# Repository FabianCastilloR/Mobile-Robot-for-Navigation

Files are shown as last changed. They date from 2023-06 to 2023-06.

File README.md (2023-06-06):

# Mobile Robot for Navigation Tasks with Obstacle Avoidance using Potential Fields

This project implements a mobile robot capable of performing navigation tasks in an environment with obstacles using the potential fields algorithm. The robot is designed to autonomously move towards a goal location while avoiding obstacles in its path.

## Table of Contents

- [Introduction](#introduction)
- [Installation](#installation)
- [Usage](#usage)
- [Algorithm](#algorithm)
- [Demo](#demo)

## Introduction

The goal of this project is to develop a mobile robot that can navigate through an environment by employing the potential fields algorithm. The robot uses an ESP32 (programmed in Arduino IDE) as an UDP server that receives data from a PC client connected to a camera that's visualizing a workspace and sends the data necessary to detect obstacles in its surroundings. The PC client is programmed in Python. By calculating attractive and repulsive forces from the goal location and obstacles, respectively, the robot can plan its path and avoid collisions.

## Installation

1. Clone the repository:

   ```bash
   git clone https://github.com/FabianCastilloR/Mobile-Robot-for-Navigation.git
   ```

2. Install the necessary dependencies in python's PC client:

   ```bash
   pip install matplotlib
   pip install numpy
   pip install opencv-contrib-python
   ```

3. Install the necessary libraries and boards in Arduino IDE:

   ```bash
   Libraries:

   MPU6050.h from https://github.com/jrowberg/i2cdevlib/tree/master/Arduino/MPU6050

   I2Cdev.h from https://github.com/jrowberg/i2cdevlib/tree/master/Arduino/I2Cdev

   Wifi.h from Arduino IDE Library Manager

   Boards:

   ESP32 from https://dl.espressif.com/dl/package_esp32_index.json

   You can add the ESP32 board to Arduino IDE by going to File > Preferences > Additional Boards Manager URLs and adding the link above.
   ```

4. Configure the robot hardware by connecting sensors and actuators appropriately.

   ```bash
   The robot hardware consists of the following components:

    - ESP32 microcontroller

    - MPU6050 IMU

    - 4 DC motors with incremental encoders (In this project we use 2 microgeared motors of 6VDC at 100RPM and 2 microgeared motors of 6VDC at 50RPM, both with 14 CPR encoders)

    - 2 motor drivers (In this project we use 2 VNH2SP30 motor drivers)

    - 1 LiPo battery (In this project we use a 3S 11.1V 2200mAh LiPo battery)

    - 1 5V voltage regulator (In this project we use a XL4005 voltage regulator)

    - 1 6V voltage regulator (In this project we use a LM2596 voltage regulator)
    
    - 1 camera (In this project we use a Razer Kiyo X camera)
   ```

5. Configure the robot software by setting the appropriate parameters in the PC_Client_WMultipleObstacles.py file.

## Usage

1. Launch the robot navigation python program:

   ```bash
   python PC_Client_WMultipleObstacles.py
   ```

2. Launch the robot navigation program in Arduino IDE:

   ```bash
    ESP32_Server_WMultipleObstacles.ino
    ```

3. Set the goal location for the robot manually.

4. Set the obstacles in the workspace manually.

5. Observe the robot's movement and obstacle avoidance behavior in the environment.

## Algorithm

The potential fields algorithm works by simulating forces acting on the robot. The robot experiences an attractive force towards the goal location and repulsive forces from nearby obstacles. By summing these forces and calculating the resultant direction, the robot can navigate towards the goal while avoiding obstacles.

The algorithm consists of the following steps:

1. Obtain the position of the robot, goal and obstacles from the artificial vision system to detect and measure the distance from the robot to the goal location and to the obstacles.

2. Calculate the attractive force towards the goal location based on the current position.

3. Calculate the repulsive forces from nearby obstacles based on their positions and distances.

4. Sum the attractive and repulsive forces to obtain the resultant force vector.

5. Update the robot's velocity and heading based on the resultant force.

6. Repeat the process iteratively to navigate towards the goal while avoiding obstacles.

## Demo

Demonstration videos of the robot's navigation capabilities can be found here:
- [Mobile Robot for Navigation Tasks with Potential Fields Demo 1](https://youtu.be/NOnhNL_rm1k)    
- [Mobile Robot for Navigation Tasks with Potential Fields Demo 2](https://youtube.com/shorts/4KPQuJDRXes?feature=share)

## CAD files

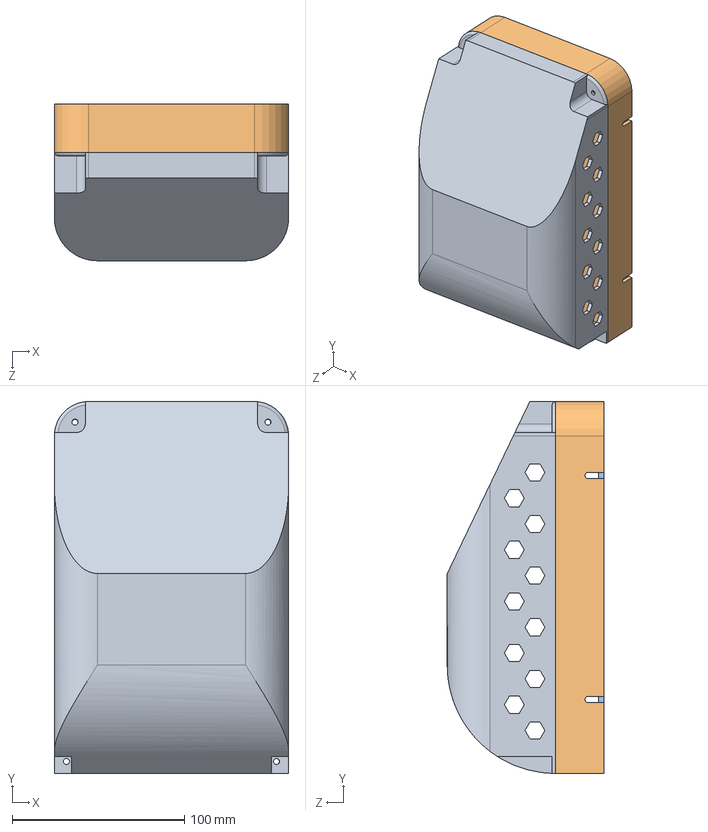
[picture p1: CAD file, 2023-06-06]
Mobile Robot CAD/Robot-Assembly.SLDASM
136.2 x 216.2 x 91.0 mm

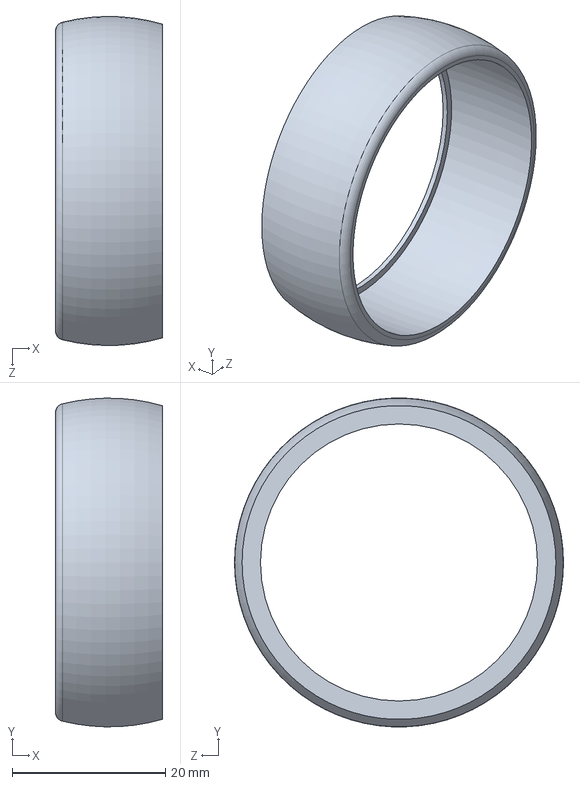
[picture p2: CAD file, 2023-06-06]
Mobile Robot CAD/Wheel.SLDPRT
14.0 x 43.0 x 43.0 mm

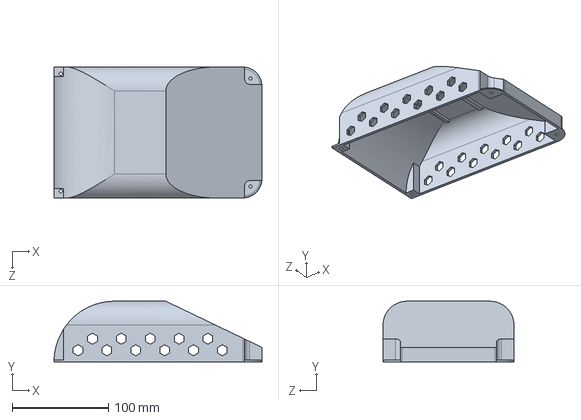
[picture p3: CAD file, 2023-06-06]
Mobile Robot CAD/Part3.SLDPRT
216.2 x 63.0 x 136.2 mm

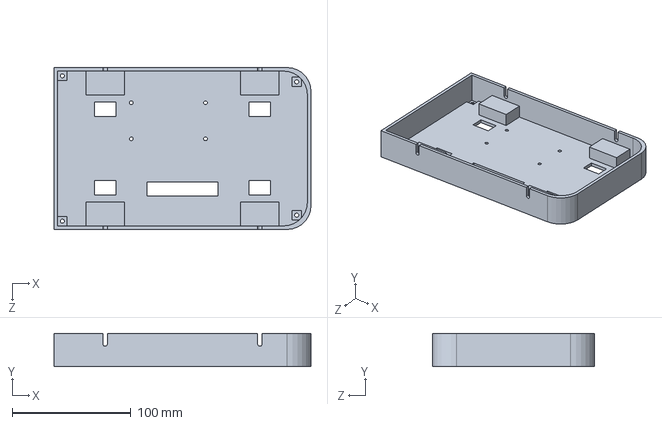
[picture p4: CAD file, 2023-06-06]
Mobile Robot CAD/Part2.SLDPRT
216.2 x 28.0 x 136.2 mm

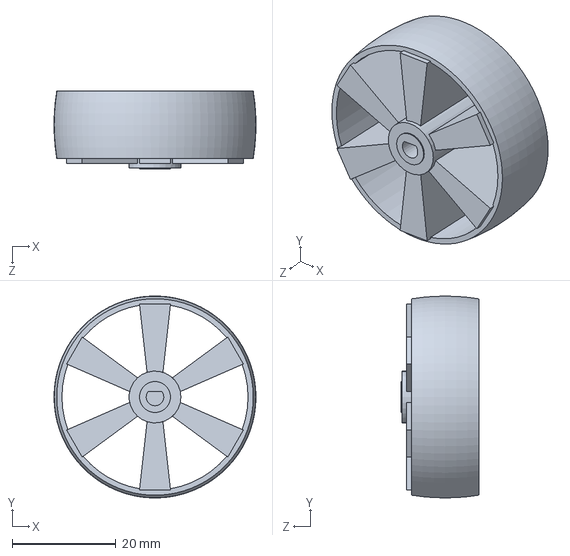
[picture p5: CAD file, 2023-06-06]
Mobile Robot CAD/Wheel-Rim.SLDPRT
38.9 x 38.9 x 15.0 mm

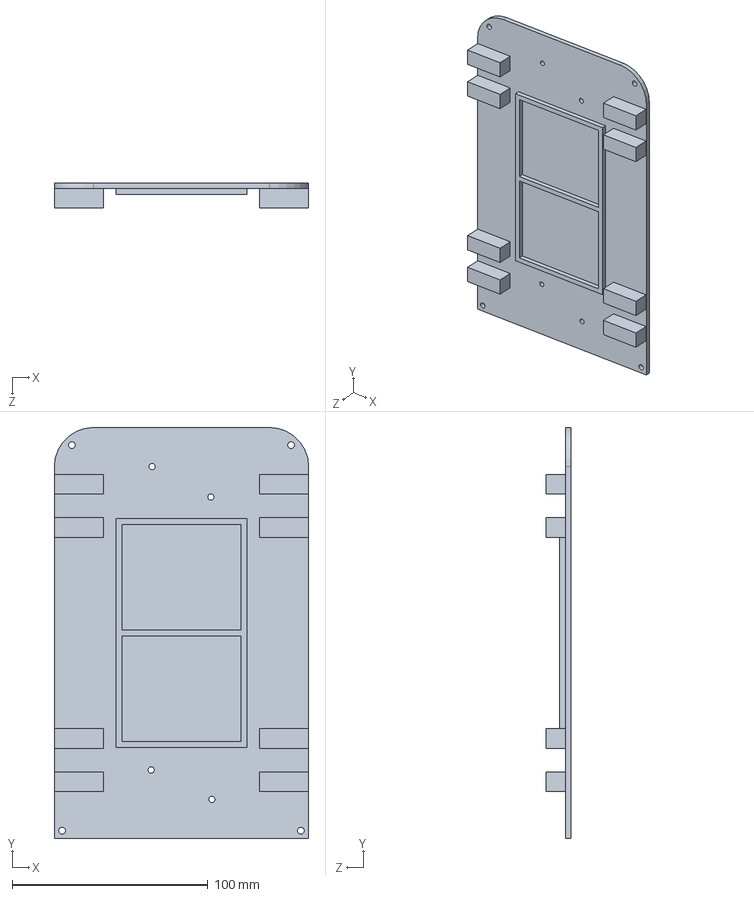
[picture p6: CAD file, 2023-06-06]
Mobile Robot CAD/Part1.SLDPRT
130.0 x 210.0 x 13.0 mm

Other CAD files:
Mobile Robot CAD/Part1.STL
Mobile Robot CAD/Part2.STL
Mobile Robot CAD/Part3.STL

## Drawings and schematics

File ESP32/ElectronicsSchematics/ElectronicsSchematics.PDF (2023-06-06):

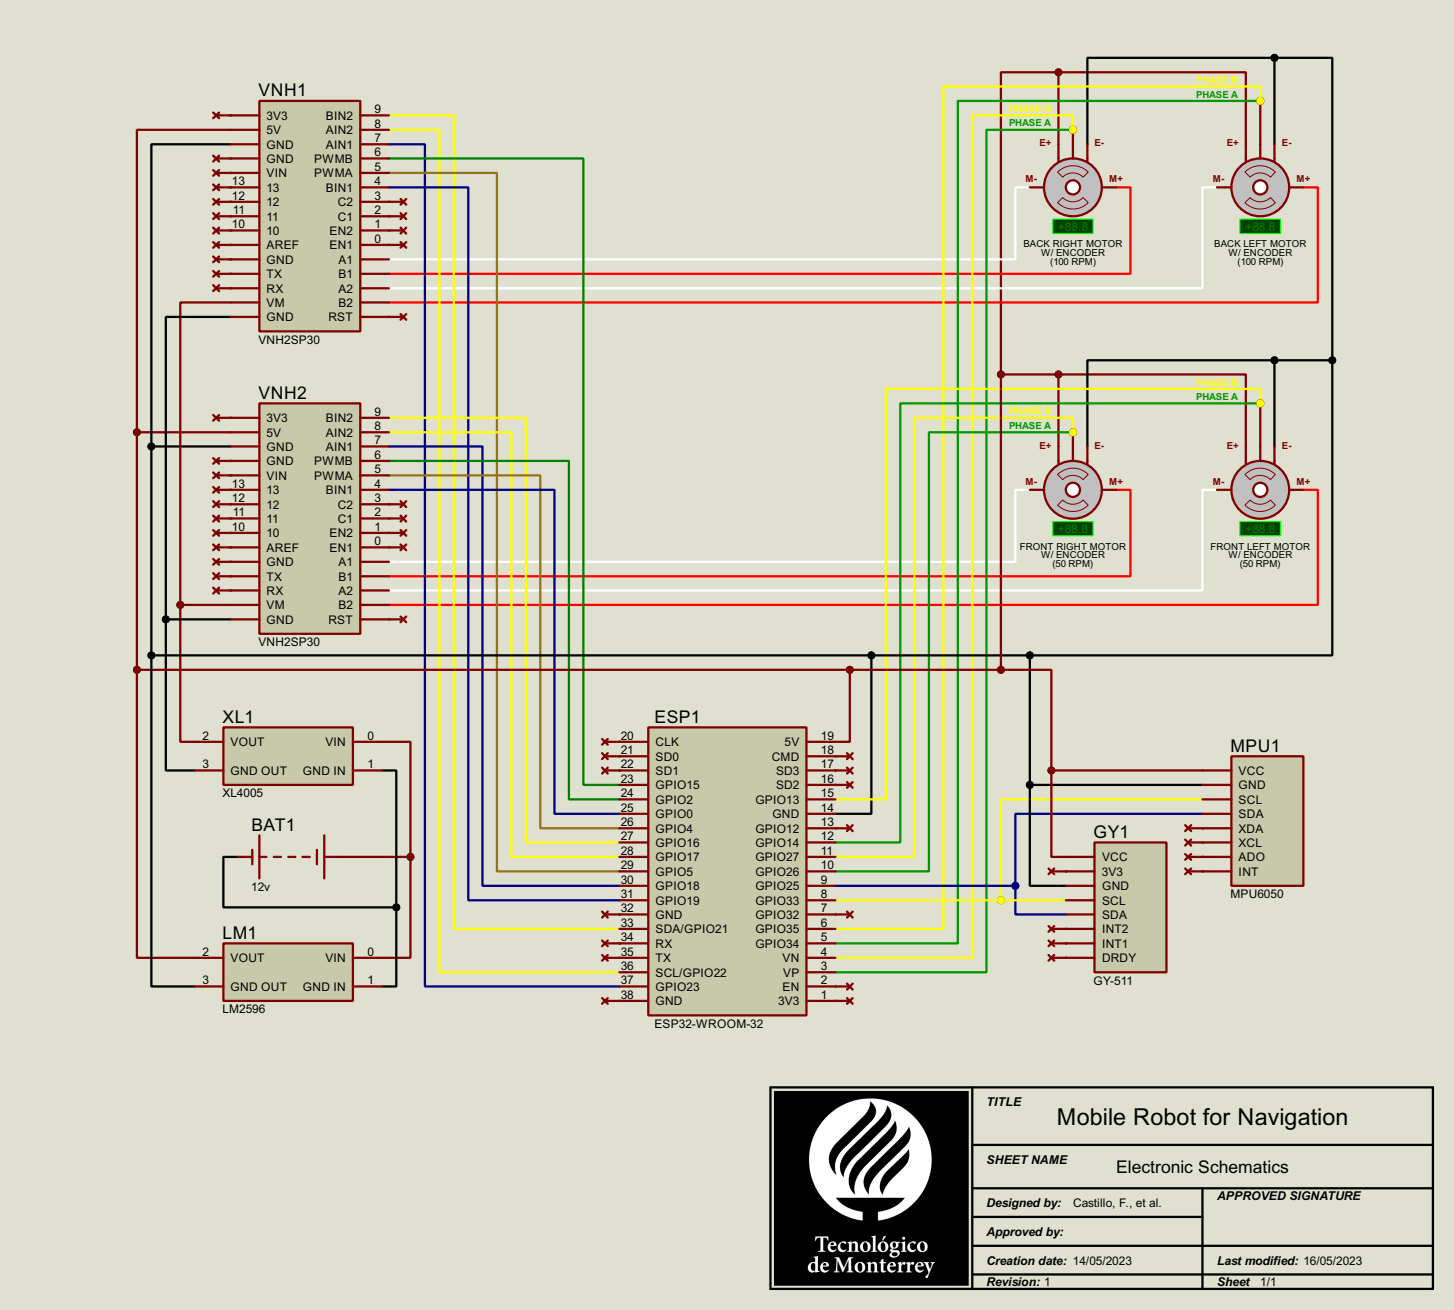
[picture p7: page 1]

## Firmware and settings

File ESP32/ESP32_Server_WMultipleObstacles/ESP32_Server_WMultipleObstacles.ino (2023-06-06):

// ESP32_Server_WMultipleObstacles.ino >

/*
Authors: F. Castillo-Rodríguez, S. Almaguer-Martínez, E. Silva-Estevez & A. Saavedra-Ricalde
Date: 2023/06/06
For Instituto Tecnológico y de Estudios Superiores de Monterrey, Campus Estado de México
Project: "Mobile Robot for Navigation Tasks"

Description:

This code is the server for the mobile robot. The communication between the client and the server is through UDP protocol.
This code receives the position (x, y) in cm of the robot, the goal and the obstacles from the client and uses it to 
determine the speed of the motors through the analysis of its kinematics. This case uses the form 
qd = J^-1 * (K1 * vti + K2 * vijo) where qd is the desired speed of the motors (linear and angular), J is the Jacobian 
matrix, vti is the speed vector of the robot and vijo is the sum of the speed vectors of each obstacle. 

For the obstacle avoidance, the robot uses the potential field method, where the robot is attracted to the goal and
repelled by the obstacles. The robot also uses a PID controller to control the speed of the motors.

The robot uses the gyroscope MPU6050 to determine its yaw angle and the encoders to determine its linear speed. It also
uses the Monster Motor Shield to control the motors. 

This code works only with Python's client code "PC_Client_WMultipleObstacles.py". To take into account only one obstacle,
the user must use the server code "ESP32_Server_WOneObstacle.ino" with the client code "PC_Client_WOneObstacle.py". To skip
obstacle avoidance, the user must use the server code "ESP32_Server_WNoObstacles.ino" with the client code 
"PC_Client_WNoObstacles.py".
*/

#include <WiFiUdp.h>
#include <MPU6050.h>  // From: https://github.com/jrowberg/i2cdevlib/tree/master/Arduino/MPU6050
#include <I2Cdev.h>   // From: https://github.com/jrowberg/i2cdevlib/tree/master/Arduino/I2Cdev
#include <Wire.h>
#include <WiFi.h>
#include <math.h>
#include <stdlib.h>

// Front right and left motor 50 RPM (298:1 reductor)
// Back right and left motor 100 RPM (149:1 reductor)

///////////////////////////////////////////////////////// Variables /////////////////////////////////////////////////////////////////////

// Define PWM pins for motors
const int motorPWMFL = 2;   // PIN 6 FRONT MOTOR SHIELD TO PIN 2 ESP32 // GREEN
const int motorPWMFR = 4;   // PIN 5 FRONT MOTOR SHIELD TO PIN 4 ESP32 // BROWN
const int motorPWMBL = 15;  // PIN 6 BACK MOTOR SHIELD TO PIN 15 ESP32 // GREEN
const int motorPWMBR = 5;   // PIN 5 BACK MOTOR SHIELD TO PIN 5 ESP32 // BROWN

// Define direction of wheels pins
const int dirFrontMFL = 0;   // PIN 4 FRONT MOTOR SHIELD TO PIN 0 ESP32 // BLUE
const int dirBackMFL = 16;   // PIN 9 FRONT MOTOR SHIELD TO PIN 16 ESP32 // YELLOW
const int dirFrontMFR = 17;  // PIN 8 FRONT MOTOR SHIELD TO PIN 17 ESP32 // YELLOW
const int dirBackMFR = 18;   // PIN 7 FRONT MOTOR SHIELD TO PIN 18 ESP32 // BLUE
const int dirFrontMBL = 19;  // PIN 4 BACK MOTOR SHIELD TO PIN 19 ESP32 // BLUE
const int dirBackMBL = 21;   // PIN 9 BACK MOTOR SHIELD TO PIN 21 ESP32 // YELLOW
const int dirFrontMBR = 22;  // PIN 8 BACK MOTOR SHIELD TO PIN 22 ESP32 // YELLOW
const int dirBackMBR = 23;   // PIN 7 BACK MOTOR SHIELD TO PIN 23 ESP32 // BLUE

// Define encoder pins
const int encoderMFL1 = 13;  // YELLOW
const int encoderMFL2 = 14;  // GREEN
const int encoderMFR1 = 27;  // YELLOW
const int encoderMFR2 = 26;  // GREEN
const int encoderMBL1 = 35;  // YELLOW
const int encoderMBL2 = 34;  // GREEN
const int encoderMBR1 = 39;  // VN PIN; YELLOW
const int encoderMBR2 = 36;  // VP PIN; GREEN

// Variables for PWM dispatch
const int pwmFrequency = 20000;  // The frequency managed by Monster Motor Shield is 20kHz
const int pwmResolution = 8;     // With a resolution of 8-bits the value goes from 0 - 255
const int pwmChannelMFL = 0;
const int pwmChannelMFR = 2;
const int pwmChannelMBL = 1;
const int pwmChannelMBR = 3;
int pwmMFL, pwmMFR, pwmMBL, pwmMBR;

// Variables for WiFi connection
WiFiUDP udp;
const char* ssid = "Conectate y di que eres mi perra";  // Your network SSID (name)
const char* password = "soytuperra";                    // Your network password
unsigned int localUdpPort = 4210;                       // Local port to listen on
char incomingPacket[1024];                              // Buffer to hold incoming packet
char buf[255];                                          // Buffer to hold outgoing packet

// Variables for yaw detection through the gyroscope
MPU6050 accgyro;
int16_t gx, gy, gz;
double gyroYaw = 0, gyroYawRad = 0, prevdTGyro = 0;

// Variables for robot's position control
double hxRobCM = 0, hyRobCM = 0, hxGoalCM = 0, hyGoalCM = 0, hxObsCM = 0, hyObsCM = 0;
int isRobot = 0, isGoal = 0, isObstacle = 0, numObs = 0;
const int maxObs = 50;
double hxMObsCM[maxObs], hyMObsCM[maxObs], hxyObsCM[maxObs * 2], vijoMag[maxObs], posObs[maxObs][2];
char hxyObsCMChar[1024];
char* variables;

// Variables for speed adcquisition
double speedRPMMFL = 0, speedRPMMFR = 0, speedRPMMBL = 0, speedRPMMBR = 0;
double speedRadSMFL = 0, speedRadSMFR = 0, speedRadSMBL = 0, speedRadSMBR = 0;
volatile int prevEncodedMFL = 0, prevEncodedMFR = 0, prevEncodedMBL = 0, prevEncodedMBR = 0;
volatile double encoderValueMFL = 0, encoderValueMFR = 0, encoderValueMBL = 0, encoderValueMBR = 0;
double prevEncoderValueMFL = 0, prevEncoderValueMFR = 0, prevEncoderValueMBL = 0, prevEncoderValueMBR = 0;
double prevMillisMFL = 0, prevMillisMFR = 0, prevMillisMBL = 0, prevMillisMBR = 0;

// Variables for PID controller
double kpMFL = 6.50, kpMFR = 15.00, kpMBL = 6.50, kpMBR = 6.50;
double kiMFL = 0.00275, kiMFR = 0.0038, kiMBL = 0.00275, kiMBR = 0.002;
double kdMFL = 5.51, kdMFR = 6.46, kdMBL = 5.51, kdMBR = 0.20;
double desiredSpeedRPMMFL = 0, desiredSpeedRPMMFR = 0, desiredSpeedRPMMBL = 0, desiredSpeedRPMMBR = 0;
double integralMFL = 0, integralMFR = 0, integralMBL = 0, integralMBR = 0;
double prevErrorMFL = 0, prevErrorMFR = 0, prevErrorMBL = 0, prevErrorMBR = 0;
int prevPIDMFL = 0, prevPIDMFR = 0, prevPIDMBL = 0, prevPIDMBR = 0;
double prevdTMFL = 0, prevdTMFR = 0, prevdTMBL = 0, prevdTMBR = 0;

/////////////////////////////////////////////////////////////////////////////////////////////////////////////////////////////////////////


///////////////////////////////////////////////////////// Program Setup /////////////////////////////////////////////////////////////////

void setup() {
  Serial.begin(115200);  // Begin serial communication at 115200 baud rate
  Wire.begin(25, 33);    // Begin I2C communication with pins SDA = 25 (Blue) and SCL = 33 (Yellow)

  // Enable encoder pins as inputs
  pinMode(encoderMFL1, INPUT);
  pinMode(encoderMFL2, INPUT);
  pinMode(encoderMFR1, INPUT);
  pinMode(encoderMFR2, INPUT);
  pinMode(encoderMBL1, INPUT);
  pinMode(encoderMBL2, INPUT);
  pinMode(encoderMBR1, INPUT);
  pinMode(encoderMBR2, INPUT);

  // Enable direction of the wheels pins as outputs
  pinMode(dirFrontMFL, OUTPUT);
  pinMode(dirBackMFL, OUTPUT);
  pinMode(dirFrontMFR, OUTPUT);
  pinMode(dirBackMFR, OUTPUT);
  pinMode(dirFrontMBL, OUTPUT);
  pinMode(dirBackMBL, OUTPUT);
  pinMode(dirFrontMBR, OUTPUT);
  pinMode(dirBackMBR, OUTPUT);

  // Configure LED PWM functionalitites
  ledcSetup(pwmChannelMFL, pwmFrequency, pwmResolution);
  ledcSetup(pwmChannelMFR, pwmFrequency, pwmResolution);
  ledcSetup(pwmChannelMBL, pwmFrequency, pwmResolution);
  ledcSetup(pwmChannelMBR, pwmFrequency, pwmResolution);

  // Attach the channel to the GPIO to be controlled
  ledcAttachPin(motorPWMFL, pwmChannelMFL);
  ledcAttachPin(motorPWMFR, pwmChannelMFR);
  ledcAttachPin(motorPWMBL, pwmChannelMBL);
  ledcAttachPin(motorPWMBR, pwmChannelMBR);

  // Interruptions of pulse detection of the encoders
  attachInterrupt(encoderMFL1, updateEncoderMFL, CHANGE);
  attachInterrupt(encoderMFL2, updateEncoderMFL, CHANGE);
  attachInterrupt(encoderMFR1, updateEncoderMFR, CHANGE);
  attachInterrupt(encoderMFR2, updateEncoderMFR, CHANGE);
  attachInterrupt(encoderMBL1, updateEncoderMBL, CHANGE);
  attachInterrupt(encoderMBL2, updateEncoderMBL, CHANGE);
  attachInterrupt(encoderMBR1, updateEncoderMBR, CHANGE);
  attachInterrupt(encoderMBR2, updateEncoderMBR, CHANGE);

  // Connect to WiFi
  Serial.printf("Connecting to %s ", ssid);
  WiFi.begin(ssid, password);  // Connect to the network
  // Wait for connection
  while (WiFi.status() != WL_CONNECTED) {
    delay(500);
    Serial.print(".");
  }
  Serial.println(" CONNECTED");
  // Print local IP address and start web server
  udp.begin(localUdpPort);
  Serial.printf("UDP Server IP: %s, UDP Server Port: %d\n", WiFi.localIP().toString().c_str(), localUdpPort);

  // Initialize gyroscope
  accgyro.initialize();
}

/////////////////////////////////////////////////////////////////////////////////////////////////////////////////////////////////////////


////////////////////////////////////////////////////////// Main Loop ////////////////////////////////////////////////////////////////////

void loop() {
  // Get the gyroscope values
  getGyroscope();
  gyroYawRad = -(gyroYaw * PI / 180);  // Convert yaw angle to radians

  // Get the speed of the wheels in RPM and rad/s with a sampling time of 50 ms
  double currentMillis = millis();
  if (currentMillis - prevMillisMFL >= 50) {
    speedRPMMFL = (-(encoderValueMFL - prevEncoderValueMFL) / ((currentMillis - prevMillisMFL) / 60000)) / (297.9238 * 14 * 2);
    speedRadSMFL = speedRPMMFL * (PI / 30);
    prevEncoderValueMFL = encoderValueMFL;
    prevMillisMFL = currentMillis;
  }
  if (currentMillis - prevMillisMFR >= 50) {
    speedRPMMFR = ((encoderValueMFR - prevEncoderValueMFR) / ((currentMillis - prevMillisMFR) / 60000)) / (297.9238 * 14 * 2);
    speedRadSMFR = speedRPMMFR * (PI / 30);
    prevEncoderValueMFR = encoderValueMFR;
    prevMillisMFR = currentMillis;
  }
  if (currentMillis - prevMillisMBL >= 50) {
    speedRPMMBL = (-(encoderValueMBL - prevEncoderValueMBL) / ((currentMillis - prevMillisMBL) / 60000)) / (297.9238 * 14);
    speedRadSMBL = speedRPMMBL * (PI / 30);
    prevEncoderValueMBL = encoderValueMBL;
    prevMillisMBL = currentMillis;
  }
  if (currentMillis - prevMillisMBR >= 50) {
    speedRPMMBR = ((encoderValueMBR - prevEncoderValueMBR) / ((currentMillis - prevMillisMBR) / 60000)) / (297.9238 * 14);
    speedRadSMBR = speedRPMMBR * (PI / 30);
    prevEncoderValueMBR = encoderValueMBR;
    prevMillisMBR = currentMillis;
  }

  // Send an empty package to the server to request the variables
  sendPackagesUDP(buf);

  // Receive the variables from the server
  variables = receivePackagesUDP();
  // Convert the variables from char to int and float to the corresponding variables
  sscanf(variables, "%d,%d,%d,%Lf,%Lf,%Lf,%Lf,%d, [%s", &isRobot, &isGoal, &isObstacle, &hxRobCM, &hyRobCM, &hxGoalCM, &hyGoalCM, &numObs, hxyObsCMChar);

  // Convert the obstacles coordinates from char to float
  getObstaclesC();

  // Get the desired speed of the wheels in RPM through its kinematic model
  getVelocityLR();

  // Determine the direction of the wheels
  wheelDirection();

  // Get the PWM of the wheels through PID control
  pwmMFL = getPID(abs(desiredSpeedRPMMFL), abs(speedRPMMFL), kpMFL, kiMFL, kdMFL, prevdTMFL, prevErrorMFL, integralMFL, prevPIDMFL);
  pwmMFR = getPID(abs(desiredSpeedRPMMFR), abs(speedRPMMFR), kpMFR, kiMFR, kdMFR, prevdTMFR, prevErrorMFR, integralMFR, prevPIDMFR);
  pwmMBL = getPID(abs(desiredSpeedRPMMBL), abs(speedRPMMBL), kpMBL, kiMBL, kdMBL, prevdTMBL, prevErrorMBL, integralMBL, prevPIDMBL);
  pwmMBR = getPID(abs(desiredSpeedRPMMBR), abs(speedRPMMBR), kpMBR, kiMBR, kdMBR, prevdTMBR, prevErrorMBR, integralMBR, prevPIDMBR);

  // Set the PWM of the wheels
  ledcWrite(pwmChannelMFL, pwmMFL);
  ledcWrite(pwmChannelMFR, pwmMFR);
  ledcWrite(pwmChannelMBL, pwmMBL);
  ledcWrite(pwmChannelMBR, pwmMBR);
}

/////////////////////////////////////////////////////////////////////////////////////////////////////////////////////////////////////////


//////////////////////////////////////////////////// Real Angle Obtention ///////////////////////////////////////////////////////////////

void getGyroscope() {
  // Get the gyroscope values
  accgyro.getRotation(&gx, &gy, &gz);

  // Get the time difference between the current and the previous gyroscope reading (Sampling time)
  double t = millis();
  double dTGyro = t - prevdTGyro;
  prevdTGyro = t;

  // Get the yaw angle in degrees, it is divided by 131 because the gyroscope has a sensitivity of 131 LSB/(°/s)
  gyroYaw += (gz / 131) * (dTGyro / 1000.0);

  // Keep the yaw angle between -180 and 180 degrees
  if (gyroYaw < 0) gyroYaw += 360;
  if (gyroYaw > 180) gyroYaw -= 360;
}

/////////////////////////////////////////////////////////////////////////////////////////////////////////////////////////////////////////


////////////////////////////////////////////////// Encoder Pulses Detection /////////////////////////////////////////////////////////////

void updateEncoderMFL() {
  // Get the encoder values in binary
  int MSB_MFL = digitalRead(encoderMFL1);  // MSB_MFL = Most significant bit
  int LSB_MFL = digitalRead(encoderMFL2);  // LSB_MFL = Least significant bit

  // Concatenate the 2 bits to get a single number
  int encodedMFL = (MSB_MFL << 1) | LSB_MFL;

  // Adding it to the previous encoded value to find the direction of rotation
  int sumMFL = (prevEncodedMFL << 2) | encodedMFL;

  // If the direction of rotation is clockwise, the encoder value decreases, otherwise it increases
  if (sumMFL == 0b1101 || sumMFL == 0b0100 || sumMFL == 0b0010 || sumMFL == 0b1011) encoderValueMFL--;
  if (sumMFL == 0b1110 || sumMFL == 0b0111 || sumMFL == 0b0001 || sumMFL == 0b1000) encoderValueMFL++;

  // Store the current encoder value for the next iteration
  prevEncodedMFL = encodedMFL;
}

void updateEncoderMFR() {
  // Get the encoder values in binary
  int MSB_MFR = digitalRead(encoderMFR1);  // MSB_MFR = Most significant bit
  int LSB_MFR = digitalRead(encoderMFR2);  // LSB_MFR = Least significant bit

  // Concatenate the 2 bits to get a single number
  int encodedMFR = (MSB_MFR << 1) | LSB_MFR;

  // Adding it to the previous encoded value to find the direction of rotation
  int sumMFR = (prevEncodedMFR << 2) | encodedMFR;

  // If the direction of rotation is clockwise, the encoder value decreases, otherwise it increases
  if (sumMFR == 0b1101 || sumMFR == 0b0100 || sumMFR == 0b0010 || sumMFR == 0b1011) encoderValueMFR--;
  if (sumMFR == 0b1110 || sumMFR == 0b0111 || sumMFR == 0b0001 || sumMFR == 0b1000) encoderValueMFR++;

  // Store the current encoder value for the next iteration
  prevEncodedMFR = encodedMFR;
}

void updateEncoderMBL() {
  // Get the encoder values in binary
  int MSB_MBL = digitalRead(encoderMBL1);  // MSB_MBL = Most significant bit
  int LSB_MBL = digitalRead(encoderMBL2);  // LSB_MBL = Least significant bit

  // Concatenate the 2 bits to get a single number
  int encodedMBL = (MSB_MBL << 1) | LSB_MBL;

  // Adding it to the previous encoded value to find the direction of rotation
  int sumMBL = (prevEncodedMBL << 2) | encodedMBL;

  // If the direction of rotation is clockwise, the encoder value decreases, otherwise it increases
  if (sumMBL == 0b1101 || sumMBL == 0b0100 || sumMBL == 0b0010 || sumMBL == 0b1011) encoderValueMBL--;
  if (sumMBL == 0b1110 || sumMBL == 0b0111 || sumMBL == 0b0001 || sumMBL == 0b1000) encoderValueMBL++;

  // Store the current encoder value for the next iteration
  prevEncodedMBL = encodedMBL;
}

void updateEncoderMBR() {
  // Get the encoder values in binary
  int MSB_MBR = digitalRead(encoderMBR1);  // MSB_MBR = Most significant bit
  int LSB_MBR = digitalRead(encoderMBR2);  // LSB_MBR = Least significant bit

  // Concatenate the 2 bits to get a single number
  int encodedMBR = (MSB_MBR << 1) | LSB_MBR;

  // Adding it to the previous encoded value to find the direction of rotation
  int sumMBR = (prevEncodedMBR << 2) | encodedMBR;

  // If the direction of rotation is clockwise, the encoder value decreases, otherwise it increases
  if (sumMBR == 0b1101 || sumMBR == 0b0100 || sumMBR == 0b0010 || sumMBR == 0b1011) encoderValueMBR--;
  if (sumMBR == 0b1110 || sumMBR == 0b0111 || sumMBR == 0b0001 || sumMBR == 0b1000) encoderValueMBR++;

  // Store the current encoder value for the next iteration
  prevEncodedMBR = encodedMBR;
}

/////////////////////////////////////////////////////////////////////////////////////////////////////////////////////////////////////////


///////////////////////////////////////////////////// UDP Communication /////////////////////////////////////////////////////////////////

char* receivePackagesUDP() {
  // Determine if there is a packet available
  int packetSize = udp.parsePacket();

  // If there is a packet available
  if (packetSize) {
    // Read the packet into the buffer
    int len = udp.read(incomingPacket, sizeof(incomingPacket) - 1);
    // If the size of the packet is greater than 0, add a null character at the end of the string
    if (len > 0) incomingPacket[len] = 0;
    // Return the packet
    return incomingPacket;
  }
}

void sendPackagesUDP(char* buf) {
  int i = 0;
  // Send the packet through the UDP connection where it received the packets from
  udp.beginPacket(udp.remoteIP(), udp.remotePort());
  // While the character is not a null character, send the character
  while (buf[i] != 0) udp.write((uint8_t)buf[i++]);
  // End the packet
  udp.endPacket();
}

/////////////////////////////////////////////////////////////////////////////////////////////////////////////////////////////////////////


//////////////////////////////////////////////// Obstacles Centroids Obtention //////////////////////////////////////////////////////////

void getObstaclesC() {
  char bufferObs[1024];
  int bufferIndex = 0;
  int i = 0;

  // Get the obstacles centroids from the string received where the obstacles centroids are separated by a comma
  for (int j = 0; j < strlen(hxyObsCMChar); j++) {
    // If the character is not a comma, add it to the buffer
    if (hxyObsCMChar[j] != ',') {
      bufferObs[bufferIndex++] = hxyObsCMChar[j];
    }
    // If the character is a comma, add a null character at the end of the buffer and convert the buffer to a double
    else {
      bufferObs[bufferIndex] = '\0';
      hxyObsCM[i] = atof(bufferObs);
      i++;
      bufferIndex = 0;
    }
  }

  // If the buffer is not empty, add a null character at the end of the buffer and convert the buffer to a double
  if (bufferIndex > 0) {
    bufferObs[bufferIndex] = '\0';
    hxyObsCM[i] = atof(bufferObs);
  }

  // Asign the x and y coordinates of the obstacles centroids to the corresponding arrays
  for (int i = 0; i < numObs; i++) {
    hxMObsCM[i] = hxyObsCM[i];
    hyMObsCM[i] = hxyObsCM[i + numObs];
  }

  // If the number of obstacles is less than the maximum number of obstacles, set the remaining obstacles centroids to 0
  for (int i = numObs; i < maxObs; i++) {
    hxMObsCM[i] = 0;
    hyMObsCM[i] = 0;
  }
}

/////////////////////////////////////////////////////////////////////////////////////////////////////////////////////////////////////////


///////////////////////////////// Left and Right Wheels Angular and Linear Velocity Obtention ///////////////////////////////////////////
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

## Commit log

2023-06-06 ESP32 Server
2023-06-06 Mobile Robot CAD
    [Part1.SLDPRT, Part1.STL, Part2.SLDPRT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]
2023-06-06 ESP32 Electronics Schematics
